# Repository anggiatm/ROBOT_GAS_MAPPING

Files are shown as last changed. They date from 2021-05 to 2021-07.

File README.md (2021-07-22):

## ROBOT GAS MAPPING





Project ini dibuat untuk bahan skripsi Ilmu Komputer Universitas Pakuan Dengan judul
**"MODEL ROBOT PENDETEKSI KUALITAS UDARA DALAM RUANGAN BERBASIS INTERNET OF THINKS (IOT)"**

Robot dilengkapi dengan sensor LiDAR untuk mendeteksi dinding disekitar robot, sensor LiDAR mengacu pada repositori yang telah dikembangkan sebelumnya
  [Low Budget Lidar by Anggiat](https://github.com/anggiatm/Low_Budget_Lidar)
  Selain itu untuk mempermudah pengembagan robot digunakan beberapa library opensource tambahan diantaranya :

<details><summary>Show !</summary>
  
  - [i2cdevlib by jrowberg](https://github.com/jrowberg/i2cdevlib)
  - [ESP-FlexyStepper by pkerspe](https://github.com/pkerspe/ESP-FlexyStepper)
</details>

#

Pada repositori ini terdapat beberapa resources yang digunakan untuk membuat robot mapping kadar gas sebuah ruangan,
diantaranya adalah :
- [source code arduino framework](https://github.com/anggiatm/ROBOT_GAS_MAPPING/blob/main/src/robot.cpp)
- [source code web interface dengan p5.js](https://github.com/anggiatm/ROBOT_GAS_MAPPING/blob/main/data/app.js)
- [3D model untuk 3D printer (.STL)](https://github.com/anggiatm/ROBOT_GAS_MAPPING/tree/main/3d-model)
- dokumentasi

Beberapa bahan bahan yang digunakan pada robot ini diantaranya :
<details>
  <summary>Show !</summary>
  
- ESP32 DEVKIT
- SENSOR MPU6050
- SENSOR VL53L0X
- SENSOR SGP30
- SENSOR MQ-2
- SENSOR DHT11
- HALL SENSOR
- STEPPER MOTOR
- DRIVER A4988
- MICRO SERVO
</details>

Kalkulasi mekanis untuk keperluan koordinat sistem / pergerakan stepper motor
KALKULASI SUDUT PUTAR ROBOT / STEP PER MM
<details>
  <summary>Show !</summary>
  
| KETERANGAN | NILAI |
| :---: | :-: |
| DIAMETER RODA (OD) | ```70 mm``` |
| DIAMETER JARAK RODA KANAN & KIRI | ```95 mm``` |
| SPEK STEPPER MOTOR | ```1.8deg/Step = 200 STEP/REVOLUTION``` | 
| MICROSTEPPING | ```1/8``` |
| MICROSTEPPING FULL ROTATION | ```200 * 8 = 1600 STEP/REVOLUTION``` |
| RUMUS KELILING LIINGKARAN | ```K = π * d``` |
| PANJANG KELILING RODA | ```π * 70 = 219.91 mm``` |
| STEP/MM BERDASARKAN KELILING RODA | ```MICROSTEPPING FULL ROTATION / PANJANG KELILING RODA  = 1600 / 219.91 = 7.28 STEPS/MM``` |
| KELILING DIAMETER RODA KANAN & KIRI | ```π x 95 = 298.45 mm``` | 
| FULL ROBOT SPIN (360deg) IN STEPS | ```KELILING DIAMETER RODA KANAN & KIRI * STEP/MM BERDASARKAN KELILING RODA = 298.45 * 7.28 = 2171.43 STEPS``` | 
| STEP/DEGREE ROBOT ROTATION | ```FULL ROBOT SPIN (360deg) IN STEPS / 360deg = 2171.43 / 360 = 6.03 STEP PER DEGREE``` | 
| MM/DEGREE ROBOT SPIN | ```KELILING DIAMETER RODA KANAN & KIRI / 360 = 298.45 / 360 = 0.83 MM PER DEGREE``` | 
</details>

Task Management menggunakan library FreeRTOS (Realtime Operating System) untuk mengatur tugas tugas yang harus dilaksanakan dalam kurun waktu tertentu
<details>
  <summary>Show !</summary>
  
| TASK FUNCTION | TASK NAME | STACK SIZE (byte) | PARAMETER | PRIORITY | TASK HANDLE | RUNNING CORE | FILE |
| :---: | :-: | :-: | :-: | :-: |  :-: | :-: | :-:  |
|_async_service_task|"async_tcp" |1024*16 |NULL |1 |&_async_service_task_handle|-1 |AsyncTCP.cpp|
|MOTOR_R->taskRunner|"FlexyStepper"|1024 |NULL |1 |MOTOR_R->xHandle |-1 |ESP_FlexyStepper.cpp|
|MOTOR_L->taskRunner|"FlexyStepper"|1024 |NULL |1 |MOTOR_L->xHandle |-1 |ESP_FlexyStepper.cpp|
|task_watch_command |"MPU_RUN_TASK"|1024*6 |NULL |1 |&watchCommand_Handle |-1 |main.cpp|
</details>

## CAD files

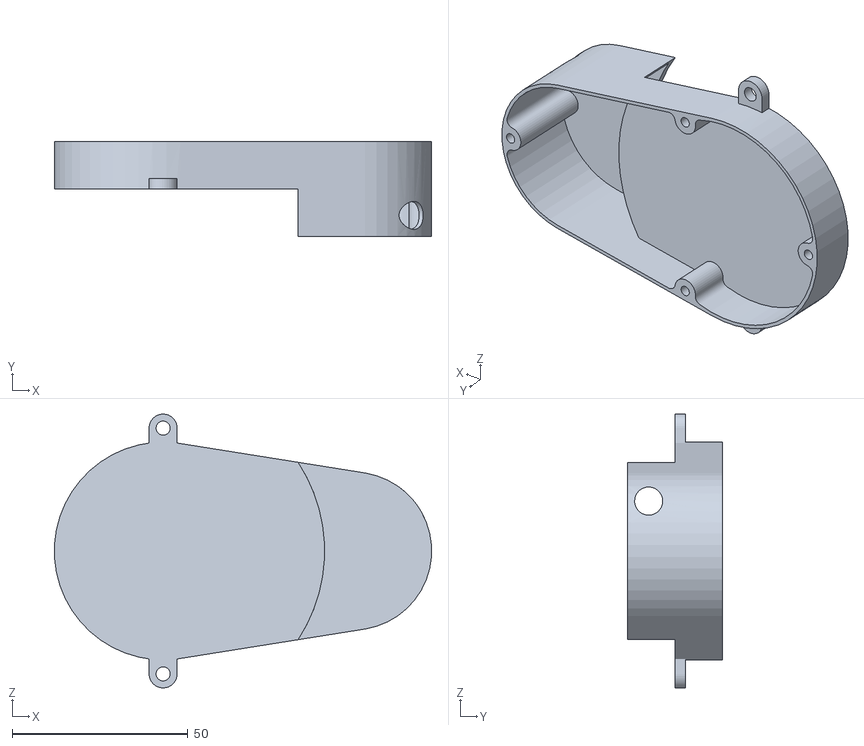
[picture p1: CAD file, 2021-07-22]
3d-model/LIDAR_BOTTOM_PALTE.STL
107.4 x 27.0 x 78.0

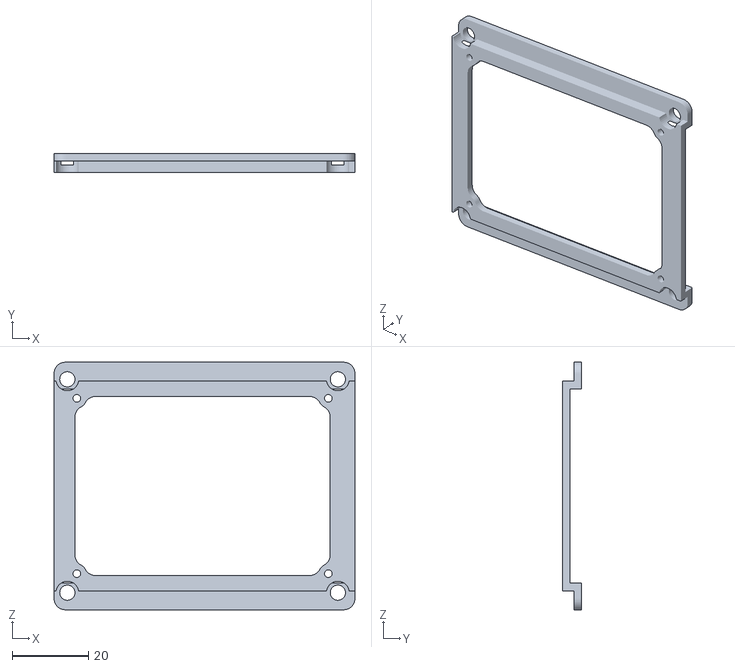
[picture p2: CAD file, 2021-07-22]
3d-model/ROBOT_MCU_PLATE.STL
79.0 x 5.00 x 65.0

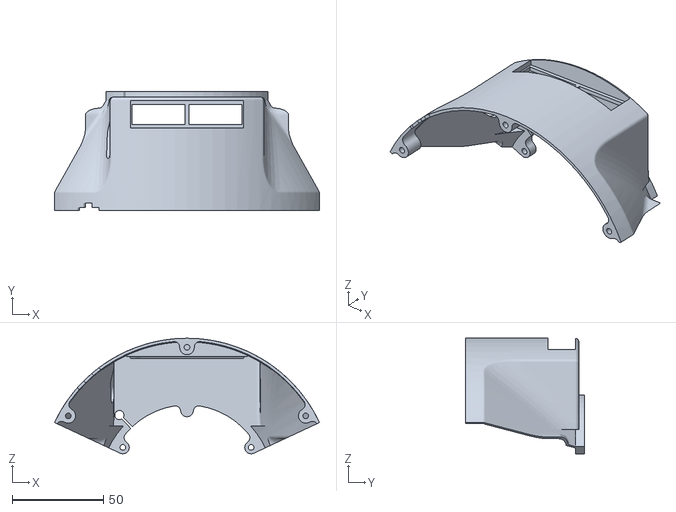
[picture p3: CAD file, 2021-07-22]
3d-model/ROBOT_BOTTOM_BACK_BODY.STL
145.0 x 65.0 x 63.2

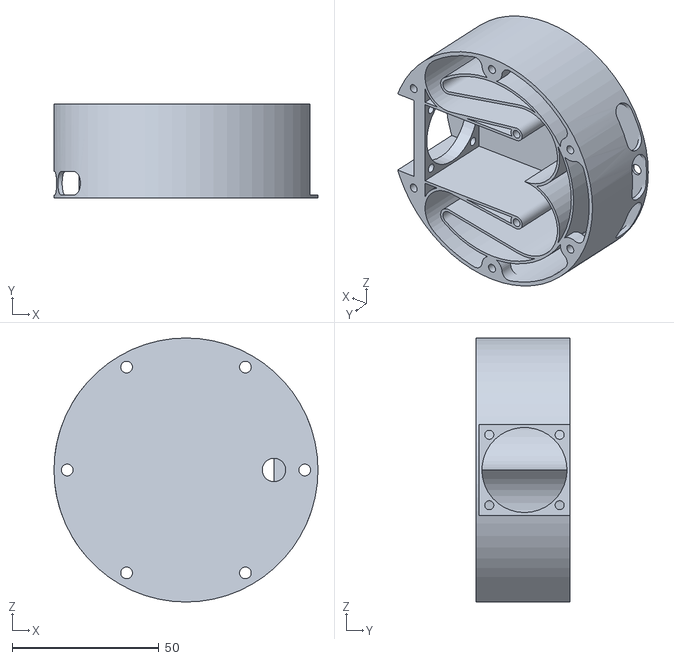
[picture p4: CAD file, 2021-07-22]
3d-model/ROBOT_E_NOSE_CHAMBER.STL
90.0 x 32.0 x 90.0

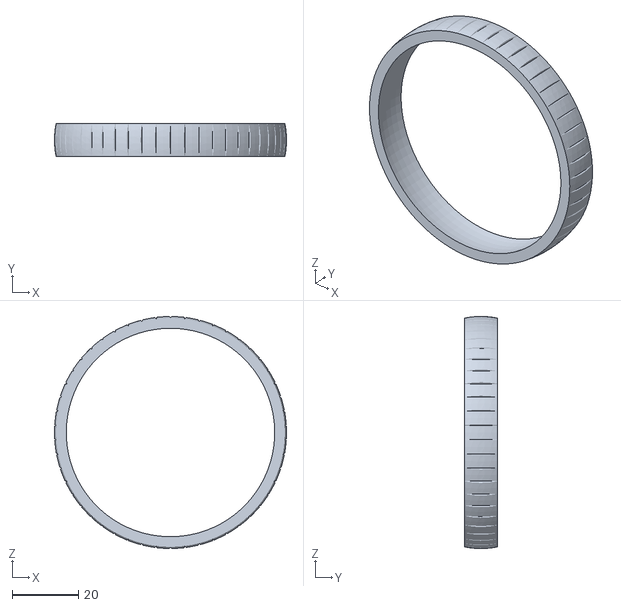
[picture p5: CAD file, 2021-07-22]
3d-model/ROBOT_TIRE_TPU.STL
70.0 x 10.0 x 70.0

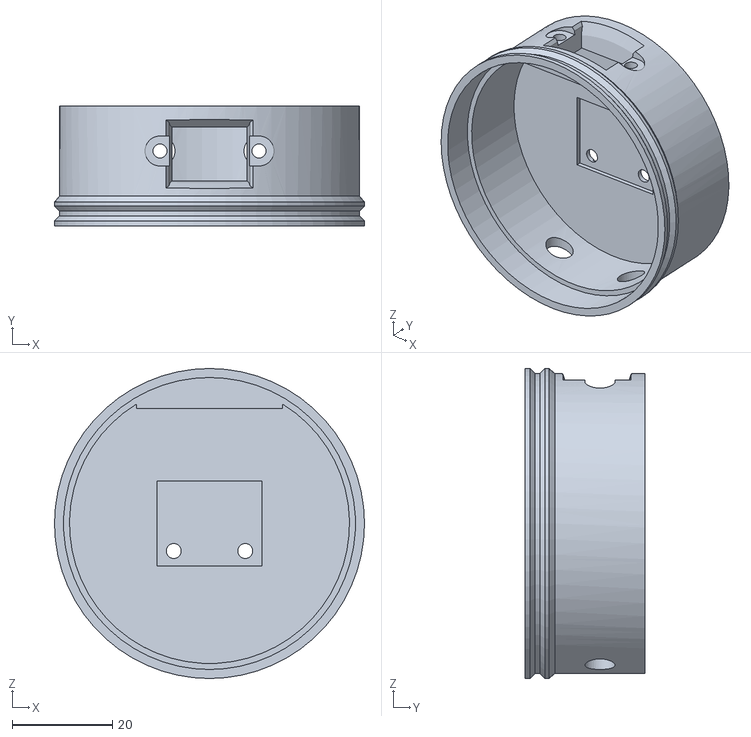
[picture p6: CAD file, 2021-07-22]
3d-model/LIDAR_TOP_PLATE.STL
62.0 x 24.0 x 62.0

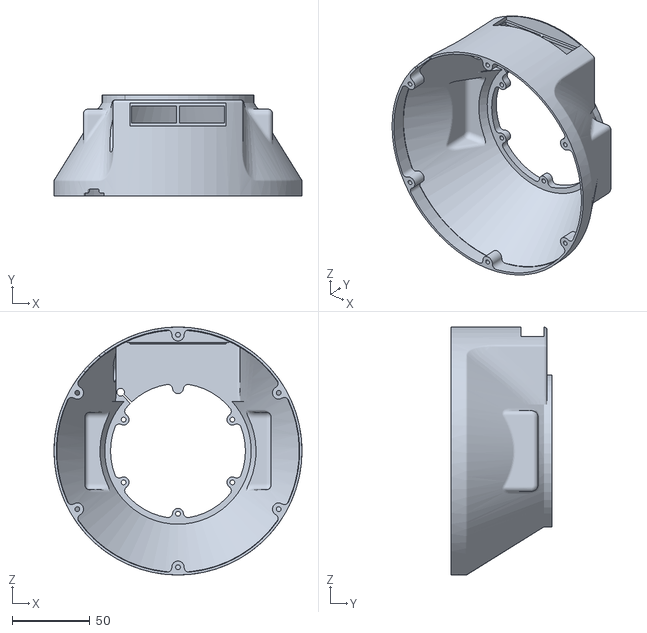
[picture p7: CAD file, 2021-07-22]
3d-model/ROBOT_BOTTOM_BODY.STL
160.0 x 65.0 x 160.0

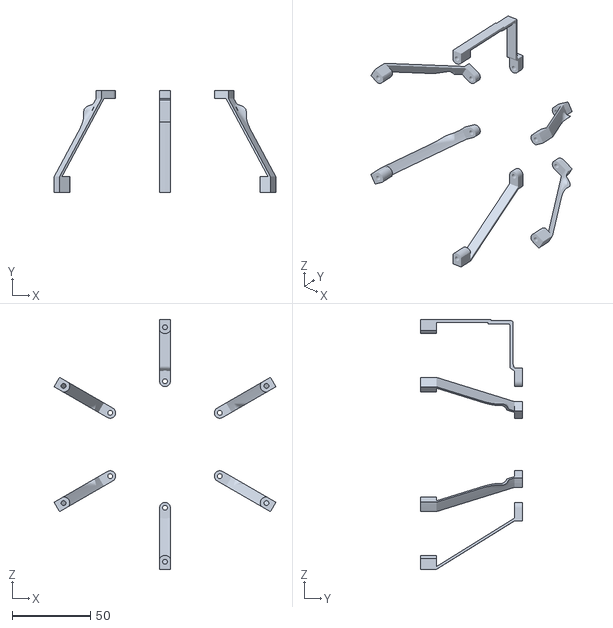
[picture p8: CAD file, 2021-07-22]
3d-model/ROBOT_BOTTOM_BODY_FRAME_ONLY.STL
141.9 x 65.0 x 160.0

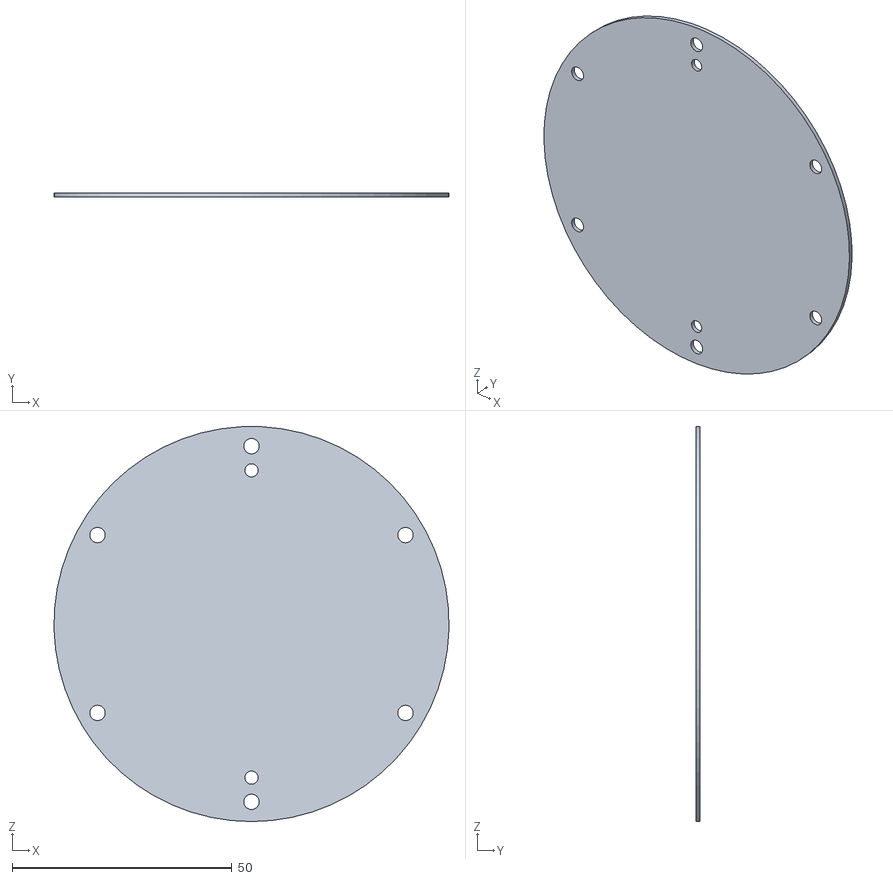
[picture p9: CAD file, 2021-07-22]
3d-model/ROBOT_TOP_PLATE.STL
90.0 x 1.00 x 90.0

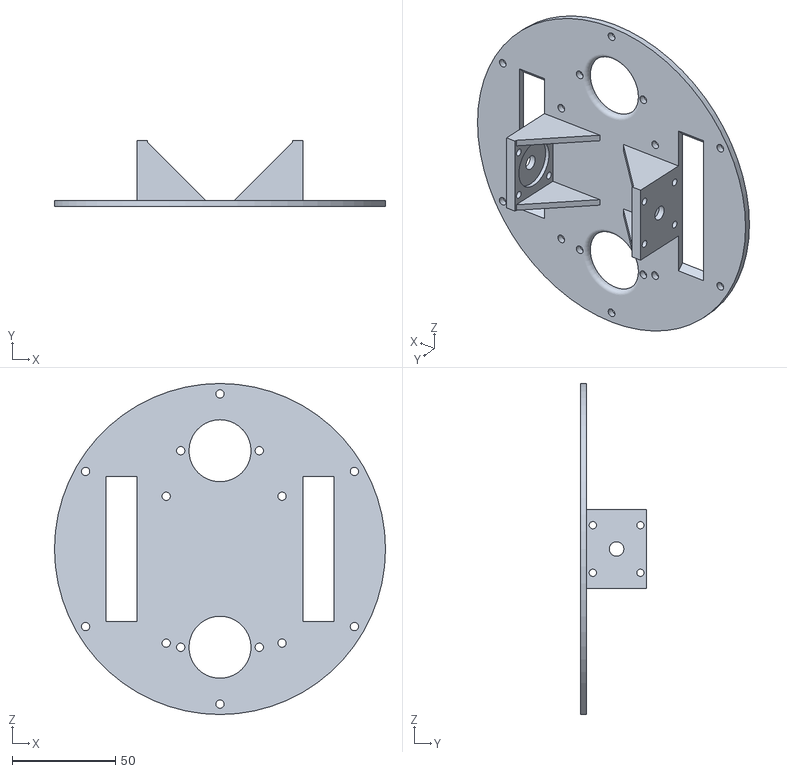
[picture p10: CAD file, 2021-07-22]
3d-model/ROBOT_BASE_PLATE.STL
160.0 x 32.0 x 160.0

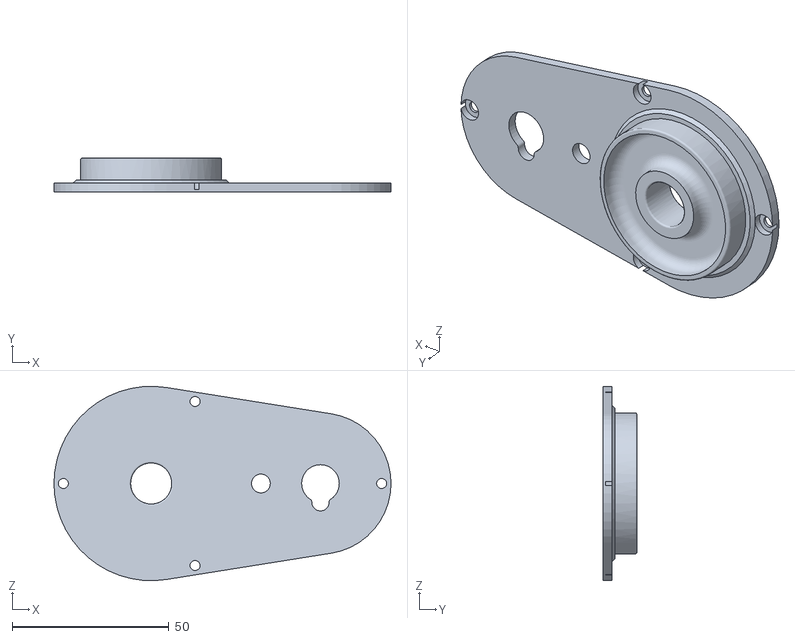
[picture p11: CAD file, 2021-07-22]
3d-model/LIDAR_MIDDLE_PLATE.STL
107.5 x 10.8 x 62.0

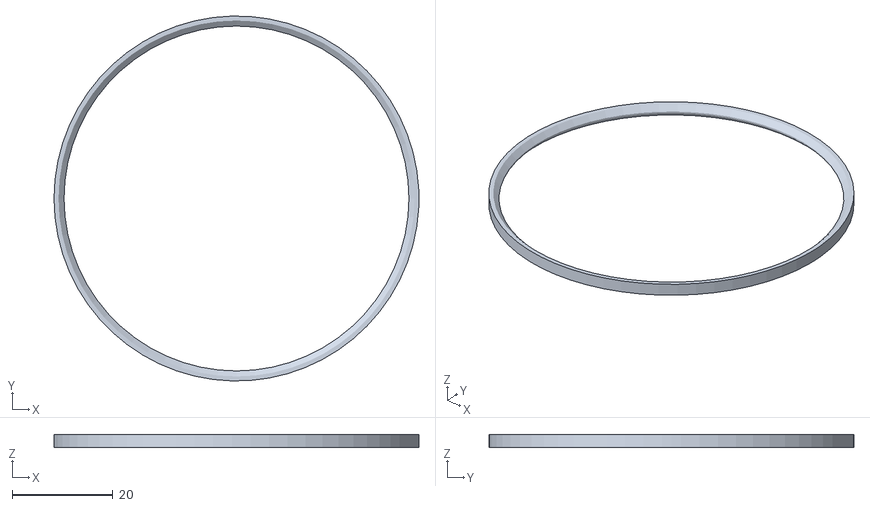
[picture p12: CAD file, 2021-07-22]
3d-model/LIDAR_TPU_BELT.STL
72.5 x 72.5 x 2.50

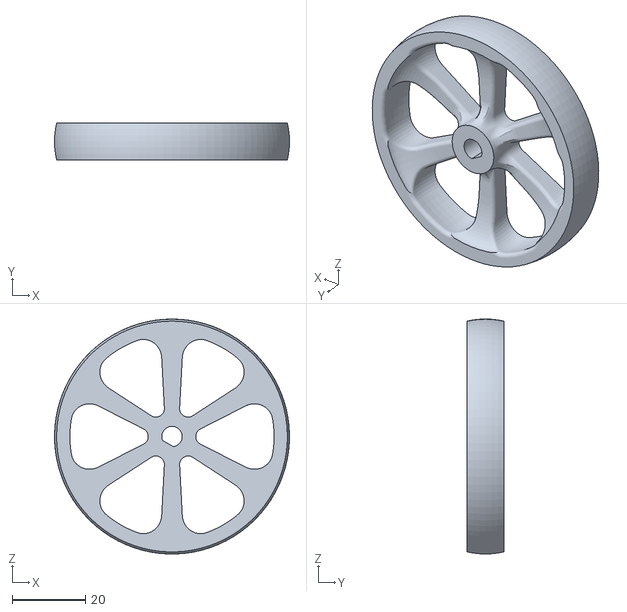
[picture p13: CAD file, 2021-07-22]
3d-model/ROBOT_WHEEL.STL
64.0 x 10.00 x 64.0

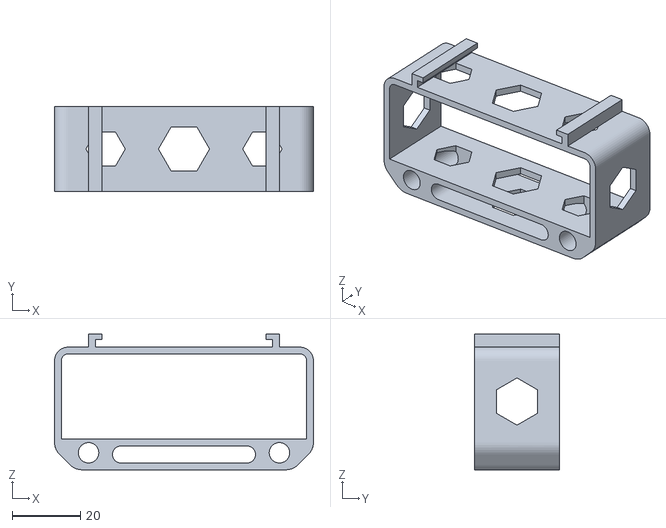
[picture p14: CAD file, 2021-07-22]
3d-model/ROBOT_BATTERY_HOLDER.STL
76.0 x 25.0 x 39.8

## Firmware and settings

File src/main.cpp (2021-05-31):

/*****************************************************************************************************************************
 * ----------------------------- KALKULASI SUDUT PUTAR ROBOT / STEP PER MM ----------------------------------------------------
 * -------------------------------------------------------------------------------------------------------------------------
 * DIAMETER RODA (OD)                     : 70MM
 * DIAMETER JARAK RODA KANAN & RODA KIRI  : 95MM
 * SPEK STEPPER MOTOR                     : 1.8deg/Step = 200 STEP PER REVOLUTION
 * MICROSTEPPING                          : 1/4
 * MICROSTEPPING FULL ROTATION            : 200 * 4 = 800 STEP PER REVOLUTION
 * RUMUS KELILING LIINGKARAN              : K = π * d
 * ---------------------------------------------------------------------------------------------------------------------------
 * PANJANG KELILING RODA                  : π * 70 = 219.91148575128552669238503682957 MM
 * 
 * STEP PER MM BERDASARKAN KELILING RODA  : MICROSTEPPING FULL ROTATION / PANJANG KELILING RODA
 *                                          = 800 / 219.91148575128552669238503682957
 *                                            3.6378272706718933890030574485145 STEPS PER MM
 * ---------------------------------------------------------------------------------------------------------------------------
 * KELILING DIAMETER RODA KANAN & KIRI    : π x 95 = 298.45130209103035765395112141155 MM
 * FULL ROBOT SPIN (360deg) IN STEPS      : KELILING DIAMETER RODA KANAN & KIRI * STEP PER MM BERDASARKAN KELILING RODA
 *                                          = 298.45130209103035765395112141155 * 3.6378272706718933890030574485145
 *                                          = 1,085.7142857142857142857142857143 STEPS
 * STEP PER DEGREE ROBOT ROTATION         : FULL ROBOT SPIN (360deg) IN STEPS / 360deg
 *                                          = 1,085.7142857142857142857142857143 / 360
 *                                          = 3.0158730158730158730158730158729 STEP PER DEGREE
 * 
 * MM PER DEGREE ROBOT SPIN               : KELILING DIAMETER RODA KANAN & KIRI / 360
 *                                          = 298.45130209103035765395112141155 / 360
 *                                          = 0.82903139469730654903875311503208 MM PER DEGREE
 * 
********************************************************************************************************************************/

/*******************************************************************************************************************************
 * ----------------------------------------------- MAIN TASK MANAGEMENT  --------------------------------------------------------------------
 * ______________________________________________________________________________________________________________________________________________________
 * |                     |                   | STACK SIZE (byte) |           |          |                             | RUNNING |                       |
 * |    TASK FUNCTION    |     TASK NAME     |  RAM CONSUMPTION  | PARAMETER | PRIORITY |          TASK HANDLE        |   CORE  |          FILE         |
 * |_____________________|___________________|___________________|___________|__________|_____________________________|_________|_______________________|
 * | _async_service_task | "async_tcp"       |     1024*15       |   NULL    |    1     | &_async_service_task_handle |   -1    | AsyncTCP.cpp          |
 * | MOTOR_R->taskRunner | "FlexyStepper"    |     1024          |   NULL*   |    1     | MOTOR_R->xHandle            |   -1    | ESP_FlexyStepper.cpp  |
 * | MOTOR_L->taskRunner | "FlexyStepper"    |     1024          |   NULL*   |    1     | MOTOR_L->xHandle            |   -1    | ESP_FlexyStepper.cpp  |
 * | task_web_client     | "WEB_CLIENT_TASK" |     1024          |   NULL    |    1     | &Client_Task_Handle);       |   -1    | main.cpp              |
 * | task_display        | "MPU_RUN_TASK"    |     1024*2        |   NULL    |    1     | &MPU_TaskRun_Handle         |   -1    | main.cpp              | DEBUG MPU
 * |_____________________|___________________|___________________|___________|__________|_____________________________|_________|_______________________|
 *                                                      
*/

// #include <Arduino.h>
#include <WiFi.h>
#include <AsyncTCP.h>
#include <ESPAsyncWebServer.h>
#include <SPIFFS.h>
#include <ESP_FlexyStepper.h>
// #include "Arduino_FreeRTOS.h"
// #include <driver/i2c.h>
// #include <esp_log.h>
// #include <esp_err.h>
// #include <freertos/FreeRTOS.h>
// #include <freertos/task.h>
#include "MPU6050_6Axis_MotionApps20.h"
// #include "sdkconfig.h"
#include <VL53L0X.h>
#include <ESP32Servo.h>
#include <ArduinoJson.h>
#include "SparkFun_SGP30_Arduino_Library.h" 

#if I2CDEV_IMPLEMENTATION == I2CDEV_ARDUINO_WIRE
    #include "Wire.h"
#endif

#ifndef M_PI
    #define M_PI 3.14159265358979323846
#endif

#define INTERRUPT_PIN 5
#define OUTPUT_READABLE_YAWPITCHROLL

//#define PIN_SDA 21
//#define PIN_SCL 22

#define STEP_PER_MM 3.637827270671893389
//#define MM_PER_DEGREE 0.82903139469730654904   //95mm Diameter
#define MM_PER_DEGREE 0.84648468721724984481     //97mm Diameter

#define DIR_R 32
#define STEP_R 33
#define DIR_L 25
#define STEP_L 26

// #define SPEED_MM_PER_SECOND 35
#define SPEED_STEP_PER_SECOND 100

#define SERVO_NEUTRAL 99
#define SERVO_RUN_CW 94
#define SERVO_RUN_ALIGNMENT 96

#define HALL_SENSOR 19  // INVERTED !!! || ON = 0 || OFF = 1
#define LED 2

//#define MM_PER_DEGREE 0.82903139469730654904

ESP_FlexyStepper MOTOR_R;
ESP_FlexyStepper MOTOR_L;

//TaskHandle_t MPU_TaskInit_Handle;
TaskHandle_t MPU_TaskRun_Handle;
TaskHandle_t Client_Task_Handle;

VL53L0X sensor;
Servo motor;
MPU6050 mpu;
SGP30 SENSOR_VOC;

// StaticJsonDocument<9216> doc;
DynamicJsonDocument doc(9216); // fixed size 9216
JsonObject root = doc.to<JsonObject>();
char buffer[9216]; // create temp buffer

bool dmpReady = false;
uint8_t mpuIntStatus;   // holds actual interrupt status byte from MPU
uint8_t devStatus;
uint16_t packetSize;
uint16_t fifoCount;     // count of all bytes currently in FIFO
uint8_t fifoBuffer[64]; // FIFO storage buffer

int angle;
int angle_old = 0;
int scanTask;
uint16_t count;
bool hall_detect;

Quaternion q;           // [w, x, y, z]         quaternion container
VectorFloat gravity;    // [x, y, z]            gravity vector
float ypr[3];           // [yaw, pitch, roll]   yaw/pitch/roll container and gravity vector

// const char* ssid = "RP";
// const char* password = "rumahpenelitian123";

const char* ssid = "MIX";
const char* password = "123456789";

// Create AsyncWebServer object on port 80
AsyncWebServer server(80);
AsyncWebSocket ws("/ws");

String splitString(String data, char separator, int index){
  int found = 0;
  int strIndex[] = {0, -1};
  int maxIndex = data.length()-1;

  for(int i=0; i<=maxIndex && found<=index; i++){
    if(data.charAt(i)==separator || i==maxIndex){
      found++;
      strIndex[0] = strIndex[1]+1;
      strIndex[1] = (i == maxIndex) ? i+1 : i;
    }
  }
  return found>index ? data.substring(strIndex[0], strIndex[1]) : "";
}

void sendHeading(){
  ws.textAll(String("heading-value"));
}

void forward(int target){
  MOTOR_R.resumeService();
  MOTOR_L.resumeService();
  long target_step = target*STEP_PER_MM;

  MOTOR_R.setCurrentPositionInSteps(0);
  MOTOR_L.setCurrentPositionInSteps(0);
  MOTOR_R.setTargetPositionInSteps(target_step);
  MOTOR_L.setTargetPositionInSteps(target_step);

  while (MOTOR_L.getCurrentPositionInSteps() != target_step && MOTOR_R.getCurrentPositionInSteps() != target_step){
    Serial.print("DEBUG : MOTOR RUNNING !! POS = ");
    Serial.println(MOTOR_L.getCurrentPositionInSteps());
    // Serial.println(MOTOR_L.getTaskStackHighWaterMark());
  }
  
  MOTOR_R.suspendService();
  MOTOR_L.suspendService();
}

void setHeading(int target){
  MOTOR_R.resumeService();
  MOTOR_L.resumeService();
  long target_step = target*STEP_PER_MM;

  MOTOR_R.setCurrentPositionInSteps(0);
  MOTOR_L.setCurrentPositionInSteps(0);
  MOTOR_R.setTargetPositionInMillimeters(-target_step);
  MOTOR_L.setTargetPositionInMillimeters(target_step);

  while (MOTOR_L.getCurrentPositionInSteps() != target_step && MOTOR_R.getCurrentPositionInSteps() != -target_step){
    Serial.print("DEBUG : MOTOR RUNNING !! POS = ");
    Serial.println(MOTOR_L.getCurrentPositionInSteps());
    // Serial.println(MOTOR_L.getTaskStackHighWaterMark());
  }
  MOTOR_R.suspendService();
  MOTOR_L.suspendService();
}

int getAngle(){
    // int mapa;
    mpu.dmpGetCurrentFIFOPacket(fifoBuffer);
    mpu.dmpGetQuaternion(&q, fifoBuffer);
    mpu.dmpGetGravity(&gravity, &q);
    mpu.dmpGetYawPitchRoll(ypr, &q, &gravity);
    // int raw = (ypr[0] * 57.2958)+180;
    // if (raw<=180){
    //     mapa = map(raw, 180, 0, 0, 180);
    // }
    // else {
    //     mapa = map(raw, 359, 181, 181, 359);
    // }
    // return mapa;
    // return raw;
    return (ypr[0] * 57.2958)+180;
}

// MPU REALTIME DEBUG
void task_display(void *pvParameters){
  (void) pvParameters;
  vTaskDelay(200);

  while (1){
    vTaskDelay(1);
    count = 0;
    int hall = 0;
    int old_hall = 0;
    
    if (scanTask > 0){
      motor.write(SERVO_RUN_CW);
      while (count <= 1){
        hall = digitalRead(HALL_SENSOR);
        if (hall != old_hall){
          old_hall = hall;
          count = count + 1;
        }
        
        angle = getAngle();
        if (angle != angle_old){
          root["a"+String(angle)] = sensor.readRangeSingleMillimeters();
          angle_old = angle;
          Serial.println(angle);
        }
      }
      
      motor.write(SERVO_NEUTRAL);
      size_t len = serializeJson(root, buffer);  // serialize to buffer
      ws.textAll(buffer, len);
      scanTask = 0;
    }
  }
  vTaskDelete(NULL);
}


void handleWebSocketMessage(void *arg, uint8_t *data, size_t len) {
  AwsFrameInfo *info = (AwsFrameInfo*)arg;
  if (info->final && info->index == 0 && info->len == len && info->opcode == WS_TEXT) {
    data[len] = 0;
    String command = splitString((char*)data, '=', 0);
    String value = splitString((char*)data, '=', 1);

    if (command == "setheading"){
      Serial.println("SET HEADING");
      int val_head = value.toInt();
      setHeading(val_head);
    }
    
    else if (command == "setforward"){
      Serial.println("SET FORWARD");
      int val_forward = value.toInt();
      forward(val_forward);
      //clearPosition();
      //sendHeading();
    }

    else if (command == "readsensor"){
      Serial.println("DEBUG : Reading Sensor..........");
      scanTask = 1;
      Serial.println("DEBUG : Read Sensor Complete..........");
    }
    
    else {
      Serial.println("UNKNOWN COMMAND");
    }
  }
}

void onEvent(AsyncWebSocket *server, AsyncWebSocketClient *client, AwsEventType type,
             void *arg, uint8_t *data, size_t len) {
  switch (type) {
    case WS_EVT_CONNECT:
      Serial.printf("WebSocket client #%u connected from %s\n", client->id(), client->remoteIP().toString().c_str());
      break;
    case WS_EVT_DISCONNECT:
      Serial.printf("WebSocket client #%u disconnected\n", client->id());
      break;
    case WS_EVT_DATA:
      handleWebSocketMessage(arg, data, len);
      break;
    case WS_EVT_PONG:
      Serial.println("WS_EVT_PONG");
      break;
    case WS_EVT_ERROR:
      Serial.println("ERROR");
      break;
  }
}

void initWebSocket() {
  ws.onEvent(onEvent);
  server.addHandler(&ws);
}

String processor(const String& var){
  Serial.println(var);
  if(var == "STATE"){
    if (1){
      return "ON";
    }
    else{
      return "OFF";
    }
  }
}

void task_web_client(void*){
	while(1){
    ws.cleanupClients();
    vTaskDelay(1);
  } 
}
volatile bool mpuInterrupt = false;
void dmpDataReady() {
    mpuInterrupt = true;
}

void sensorAlignment(){
  hall_detect = digitalRead(HALL_SENSOR);
  if (hall_detect){
    motor.write(SERVO_RUN_ALIGNMENT);
  }
  while(hall_detect){
    hall_detect = digitalRead(HALL_SENSOR);
  }
  motor.write(SERVO_NEUTRAL);
}

void setup(){
  scanTask = 0;
  #if I2CDEV_IMPLEMENTATION == I2CDEV_ARDUINO_WIRE
    Wire.begin();
    Wire.setClock(400000); 
  #elif I2CDEV_IMPLEMENTATION == I2CDEV_BUILTIN_FASTWIRE
    Fastwire::setup(400, true);
  #endif

  Serial.begin(115200);
  motor.attach(23);
  motor.write(SERVO_NEUTRAL); 
  if(!SPIFFS.begin(true)){
    Serial.println("An Error has occurred while mounting SPIFFS");
    return;
  }

  if (SENSOR_VOC.begin() == false) {
    Serial.println("No SGP30 Detected. Check connections.");
    while (1);
  }
  //Initializes sensor for air quality readings
  //measureAirQuality should be called in one second increments after a call to initAirQuality
  SENSOR_VOC.initAirQuality();

  pinMode(HALL_SENSOR, INPUT);
  pinMode(LED, OUTPUT);
  sensorAlignment();

  sensor.setTimeout(500);
  if (!sensor.init()){
      Serial.println("Failed to detect and initialize sensor!");
      while (1) {}
  }
    
  // reduce timing budget to 20 ms (default is about 33 ms)
  sensor.setMeasurementTimingBudget(20000);

  // initialize device
  Serial.println(F("Initializing I2C devices..."));
  mpu.initialize();
  pinMode(INTERRUPT_PIN, INPUT);

  Serial.println(F("Testing device connections..."));
  Serial.println(mpu.testConnection() ? F("MPU6050 connection successful") : F("MPU6050 connection failed"));

  Serial.println(F("Initializing DMP..."));
  devStatus = mpu.dmpInitialize();

  mpu.setXGyroOffset(220);
  mpu.setYGyroOffset(76);
  mpu.setZGyroOffset(0);   // -85 default
  mpu.setZAccelOffset(1888); // 1688 factory default for my test chip

  if (devStatus == 0) {
    mpu.CalibrateAccel(6);
    mpu.CalibrateGyro(6);
    mpu.PrintActiveOffsets();
    Serial.println(F("Enabling DMP..."));
    mpu.setDMPEnabled(true);
    Serial.print(F("Enabling interrupt detection (Arduino external interrupt "));
    Serial.print(digitalPinToInterrupt(INTERRUPT_PIN));
    Serial.println(F(")..."));
    attachInterrupt(digitalPinToInterrupt(INTERRUPT_PIN), dmpDataReady, RISING);
    mpuIntStatus = mpu.getIntStatus();
    Serial.println(F("DMP ready! Waiting for first interrupt..."));
    dmpReady = true;
    packetSize = mpu.dmpGetFIFOPacketSize();
  } 
  else {
    Serial.print(F("DMP Initialization failed (code "));
    Serial.print(devStatus);
    Serial.println(F(")"));
  }

  MOTOR_R.connectToPins(STEP_R, DIR_R);
  MOTOR_L.connectToPins(STEP_L, DIR_L);
  MOTOR_R.setSpeedInStepsPerSecond(SPEED_STEP_PER_SECOND);
  MOTOR_L.setSpeedInStepsPerSecond(SPEED_STEP_PER_SECOND);
  
  // Connect to Wi-Fi
  WiFi.begin(ssid, password);
  while (WiFi.status() != WL_CONNECTED) {
    delay(1000);
    Serial.println("Connecting to WiFi..");
  }
  
  initWebSocket();

  // Route for root / web page
  server.on("/", HTTP_GET, [](AsyncWebServerRequest *request){
    request->send(SPIFFS, "/index.html", String(), false, processor);
  });

  server.on("/bootstrap-grid.min.css", HTTP_GET, [](AsyncWebServerRequest *request){
    request->send(SPIFFS, "/bootstrap-grid.min.css");
  });

  server.on("/style.css", HTTP_GET, [](AsyncWebServerRequest *request){
    request->send(SPIFFS, "/style.css");
  });

  server.on("/p5.min.js", HTTP_GET, [](AsyncWebServerRequest *request){
    request->send(SPIFFS, "/p5.min.js");
  });

  server.on("/app.js", HTTP_GET, [](AsyncWebServerRequest *request){
    request->send(SPIFFS, "/app.js");
  });

  MOTOR_R.startAsService(-1);
  MOTOR_L.startAsService(-1);      

  xTaskCreateUniversal(task_display, "MPU_RUN_TASK", 1024*2, NULL, 1, &MPU_TaskRun_Handle, -1);
  server.begin();
  xTaskCreate(task_web_client, "WEB_CLIENT_TASK", 1024, NULL, 1, &Client_Task_Handle);
  //digitalWrite(ledPin, HIGH);
  delay(3000);
  dmpReady = true;
  MOTOR_R.suspendService();
  MOTOR_L.suspendService();
  digitalWrite(LED, HIGH);
  // Print ESP Local IP Address
  Serial.println(WiFi.localIP());
}

void loop() {
  delay(1000); //Wait 1 second
  //measure CO2 and TVOC levels
  SENSOR_VOC.measureAirQuality();
  Serial.print("CO2: ");
  Serial.print(SENSOR_VOC.CO2);
  Serial.print(" ppm\tTVOC: ");
  Serial.print(SENSOR_VOC.TVOC);
  Serial.println(" ppb");
}

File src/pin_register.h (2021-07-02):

// #ifndef pin_register.h
// #define pin_register.h

//#define PIN_SDA 21
//#define PIN_SCL 22

#define INTERRUPT_PIN       5

#define DIR_R               32
#define STEP_R              33
#define DIR_L               25
#define STEP_L              26
#define STEPPER_ENABLE_PIN  13

#define HALL_SENSOR         19  // INVERTED !!! || ON = 0 || OFF = 1

#define DHT11_PIN           16
#define SMOKE_SENSOR        34    // used for ESP32
#define SENSOR_BATTERY_PIN  39

#define LED_R               15
#define LED_G               2
#define LED_B               4

#define FAN_RELAY_PIN       18

// #endif

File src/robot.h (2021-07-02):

#ifndef robot_h
#define robot_h

// #include <Arduino.h>
#include <WiFi.h>
#include <AsyncTCP.h>
#include <ESPAsyncWebServer.h>
#include <SPIFFS.h>
#include <ESP_FlexyStepper.h>
#include <MPU6050_6Axis_MotionApps20.h>
#include <VL53L0X.h>
#include <ESP32Servo.h>
#include <ArduinoJson.h>
// #include "SparkFun_SGP30_Arduino_Library.h"
#include <Adafruit_SGP30.h>
#include <MQUnifiedsensor.h>
#include <battery.h>
#include <Adafruit_Sensor.h>
#include <DHT.h>
#include <DHT_U.h>
#include <pin_register.h>

#if I2CDEV_IMPLEMENTATION == I2CDEV_ARDUINO_WIRE
    #include "Wire.h"
#endif

#ifndef M_PI
    #define M_PI 3.14159265358979323846
#endif

#define OUTPUT_READABLE_YAWPITCHROLL
#define DHTTYPE DHT11   // DHT 11

// #define STEP_PER_MM 3.637827270671893389
// #define MM_PER_DEGREE 0.84648468721724984481     //97mm Diameter
#define STEP_PER_MM 7.28
#define MM_PER_DEGREE 1.69     //97mm Diameter
//#define MM_PER_DEGREE 0.82903139469730654904   //95mm Diameter

// #define SPEED_MM_PER_SECOND 35
#define SPEED_STEP_PER_SECOND 200

#define SERVO_NEUTRAL 99
#define SERVO_RUN_CW 93 //94
#define SERVO_RUN_ALIGNMENT 96

class robot {
    public:
    robot();
    ~robot();
};

#endif

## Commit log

2021-03-17 change board to esp32
2021-04-01 Add Stepper Motor
2021-05-21 add hall sensor
2021-05-31 add sensor voc
2021-06-04 add mpu calibration
2021-07-22 add 3d model
    [LIDAR_BOTTOM_PALTE.STL, LIDAR_MIDDLE_PLATE.STL, LIDAR_TOP_PLATE.STL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]

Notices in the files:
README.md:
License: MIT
